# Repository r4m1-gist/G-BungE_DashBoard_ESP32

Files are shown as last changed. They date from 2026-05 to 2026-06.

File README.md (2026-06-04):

# G-BungE Dashboard ESP32

This project is an ESP32-based dashboard for the final Baja vehicle, Mk.5.
It aims to display vehicle status on 4-digit 7-segment modules using CAN data from the Sevcon Gen4 Size 6 controller.

Firmware and hardware resources for the G-BungE Mk.5 Baja EV dashboard.

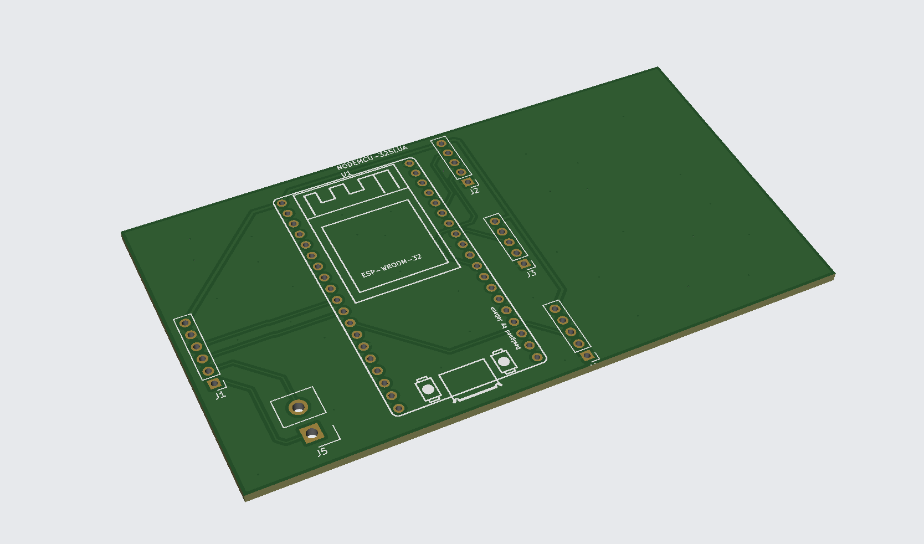
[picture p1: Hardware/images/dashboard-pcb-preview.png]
G-BungE Dashboard PCB preview


## Project Layout

```text
Firmware/
  main/
    main.ino

  test/
    ledsegmentcheck/
      ledsegmentcheck.ino

    soc_can_display/
      soc_can_display.ino

Hardware/
  README.md

  PCB KiCAD files/
    009_GBdashboard.kicad_pcb
    009_GBdashboard.kicad_pro
    009_GBdashboard.kicad_sch

    gerber/
      009_GBdashboard.zip
      info.md

  STEP files/
    DashBoard PLA Housing.step

  images/
    dashboard-pcb-preview.png
```

## Firmware

- `Firmware/main/main.ino`: main dashboard sketch for the Mk.5 vehicle
- `Firmware/test/ledsegmentcheck/ledsegmentcheck.ino`: basic check sketch for three 7-segment modules and CAN communication
- `Firmware/test/soc_can_display/soc_can_display.ino`: test sketch for displaying SoC, temperature, and voltage values received over CAN

## Hardware

- Controller: NodeMCU ESP32-S
- CAN transceiver: SN65HVD230
- Display: 4-digit 7-segment module x3
- PCB source: `Hardware/PCB KiCAD files/009_GBdashboard.kicad_pcb`, `Hardware/PCB KiCAD files/009_GBdashboard.kicad_sch`, `Hardware/PCB KiCAD files/009_GBdashboard.kicad_pro`
- Manufacturing export: `Hardware/PCB KiCAD files/gerber/009_GBdashboard.zip`
- 3D PLA housing: `Hardware/STEP files/DashBoard PLA Housing.step`

## Pin Map

### 7-Segment Display

| Part | SCLK | RCLK | DIO |
| --- | --- | --- | --- |
| SEG1 | GPIO21 | GPIO22 | GPIO17 |
| SEG2 | GPIO18 | GPIO19 | GPIO23 |
| SEG3 | GPIO13 | GPIO14 | GPIO25 |

### CAN

| Part | ESP32 Pin |
| --- | --- |
| CAN TXD / CTX | GPIO26 |
| CAN RXD / CRX | GPIO27 |

## CAN / Display Behavior

- CAN bus speed: 500 kbps
- Main sketch polls the Sevcon controller over CANopen SDO.
- Display 1 shows motor speed in rpm.
- Display 2 shows motor temperature in degrees Celsius.
- Test sketches are kept for segment wiring checks and CAN receive/display checks before vehicle installation.

## Notes

- Main firmware is built around the Sevcon Gen4 Size 6 controller used in the Mk.5 Baja EV.
- CAN bus termination should be 120 ohm only at each end of the bus.
- Segment display polarity can be adjusted in each sketch with `SEGMENT_ACTIVE_LOW`, `DIGIT_ACTIVE_HIGH`, and `SEND_SEGMENTS_FIRST`.
- Hardware PCB files were added under `Hardware/` for Mk.5 dashboard fabrication and reference.

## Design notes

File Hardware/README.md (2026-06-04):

# Hardware

Hardware resources for the G-BungE Mk.5 ESP32 dashboard.

G-BungE Dashboard PCB preview

## PCB KiCad Files

- Source files: `PCB KiCAD files/009_GBdashboard.kicad_pcb`, `PCB KiCAD files/009_GBdashboard.kicad_sch`, `PCB KiCAD files/009_GBdashboard.kicad_pro`
- Gerber export: `PCB KiCAD files/gerber/009_GBdashboard.zip`
- Made by quserunknownp.

## STEP Files

- Dashboard PLA housing: `STEP files/DashBoard PLA Housing.step`
- Made by r4m1.

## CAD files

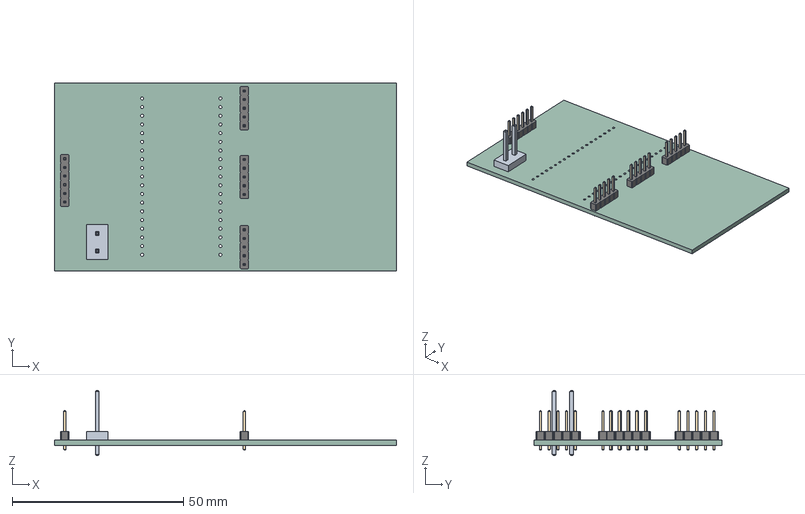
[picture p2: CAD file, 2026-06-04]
Hardware/STEP files/009_GBdashboard.step
100.0 x 55.0 x 19.1 mm
009_GBdashboard 1.1.1
PinHeader_1x05_P2.54mm_Vertical x 3
PinHeader_1x06_P2.54mm_Vertical
009_GBdashboard_PCB

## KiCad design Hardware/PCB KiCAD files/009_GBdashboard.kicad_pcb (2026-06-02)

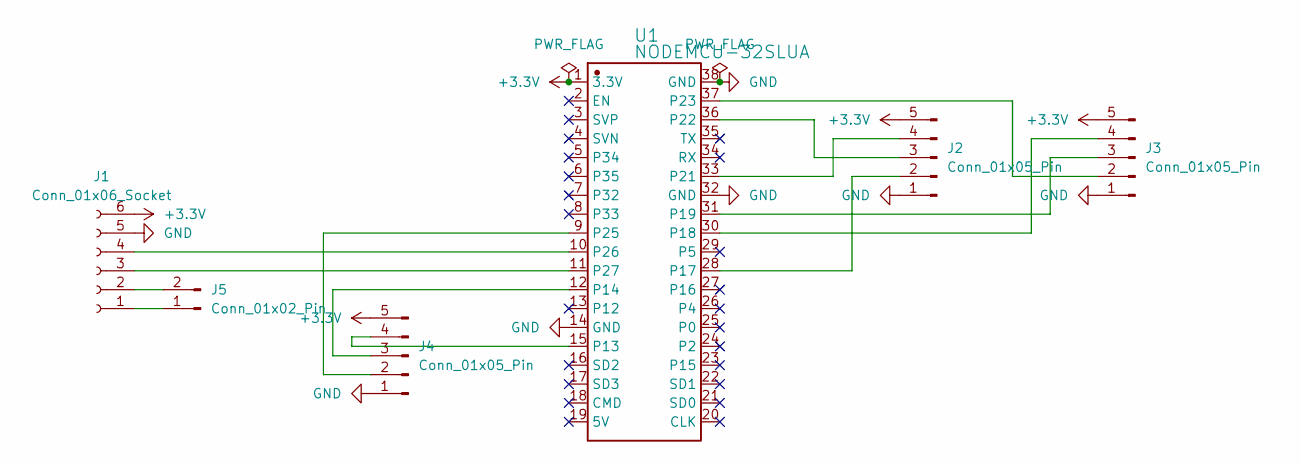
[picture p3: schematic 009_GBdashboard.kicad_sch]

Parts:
J1: Conn_01x06_Socket; PinHeader_1x06_P2.54mm_Vertical
J2, J3, J4: Conn_01x05_Pin; PinHeader_1x05_P2.54mm_Vertical
J5: Conn_01x02_Pin; Samtec_HPM-02-01-x-S_Straight_1x02_Pitch5.08mm
U1: NODEMCU-32SLUA; COMM-TH_NODEMCU-32SLUA; Manufacturer Part NodeMCU-32SLua

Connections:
+3.3V: J1.6, J2.5, J3.5, J4.5, U1.1 (3.3V)
GND: J1.5, J2.1, J3.1, J4.1, U1.14 (GND), U1.32 (GND), U1.38 (GND)
unnamed: J1.1, J5.1
unnamed: J1.2, J5.2
unnamed: J1.3, U1.11 (P27)
unnamed: J1.4, U1.10 (P26)
unnamed: J2.2, U1.28 (P17)
unnamed: J2.3, U1.36 (P22)
unnamed: J2.4, U1.33 (P21)
unnamed: J3.2, U1.37 (P23)
unnamed: J3.3, U1.31 (P19)
unnamed: J3.4, U1.30 (P18)
unnamed: J4.2, U1.9 (P25)
unnamed: J4.3, U1.12 (P14)
unnamed: J4.4, U1.15 (P13)

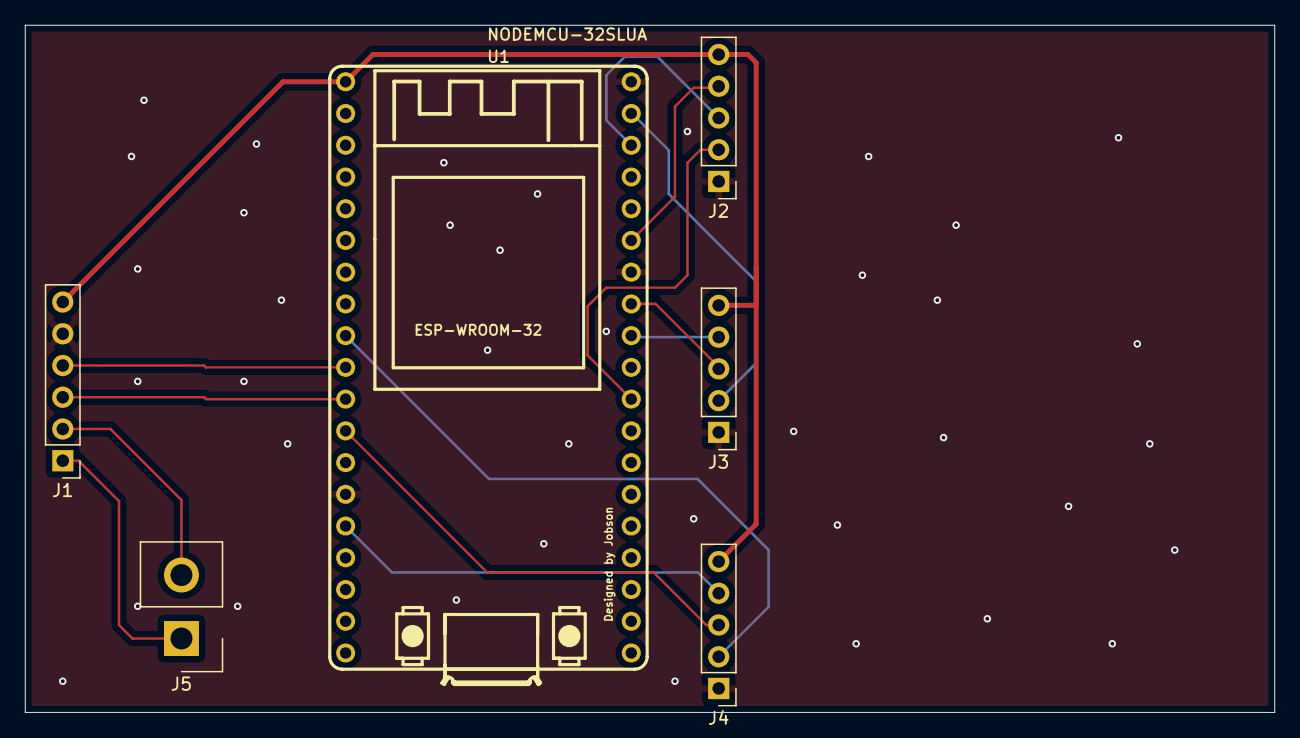
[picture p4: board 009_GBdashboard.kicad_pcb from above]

Board: 2 copper layers, 100.0 x 55.0 mm, 6 parts (0 on the bottom side), 15 nets.

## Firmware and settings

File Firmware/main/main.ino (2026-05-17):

/*
  G-BungE dashboard main sketch for Sevcon Gen4 Size 6

  Reads motor speed and motor temperature from the Sevcon over CANopen SDO.

  Display mapping:
    DISP1: motor speed, rpm, absolute value, 0..9999
    DISP2: motor temperature, degC, 0..9999

  Sevcon Gen4 manual notes:
    - Motor torque/speed are available in the 0x6000..0x67FF object range.
    - CiA 402 velocity actual value is commonly 0x606C:00.
    - Motor measurements including temperature are at object 0x4600.
    - The manual mentions motor temperature via 0x4600 sub 16 for CAN based thermistor use.

  If DVT maps these values to a TPDO later, this sketch can be changed to parse that
  PDO directly. SDO polling is intentionally used here so the dashboard can pull the
  values without depending on a preconfigured TPDO.
*/

#include <Arduino.h>
#include "freertos/FreeRTOS.h"
#include "driver/twai.h"

struct SegmentPins {
  uint8_t sclk;
  uint8_t rclk;
  uint8_t dio;
};

struct CanOpenObject {
  uint16_t index;
  uint8_t subIndex;
};

enum class PendingRequest : uint8_t {
  NONE,
  SPEED,
  MOTOR_TEMP
};

static const SegmentPins DISP1 = {21, 22, 17};
static const SegmentPins DISP2 = {18, 19, 23};

static const uint8_t CAN_TX_PIN = 26;
static const uint8_t CAN_RX_PIN = 27;

static const uint8_t SEVCON_NODE_ID = 1;
static const uint32_t SDO_REQUEST_ID = 0x600 + SEVCON_NODE_ID;
static const uint32_t SDO_RESPONSE_ID = 0x580 + SEVCON_NODE_ID;

static const CanOpenObject MOTOR_SPEED_OBJECT = {0x606C, 0x00};
static const CanOpenObject MOTOR_TEMP_OBJECT = {0x4600, 0x16};

static const uint32_t SDO_POLL_INTERVAL_MS = 100;
static const uint32_t SDO_RESPONSE_TIMEOUT_MS = 250;
static const uint32_t VALUE_TIMEOUT_MS = 2000;
static const uint32_t DISPLAY_REFRESH_INTERVAL_US = 1200;

static const bool SEGMENT_ACTIVE_LOW = true;
static const bool DIGIT_ACTIVE_HIGH = true;
static const bool SEND_SEGMENTS_FIRST = true;
static const uint16_t DIGIT_REFRESH_US = 250;

static uint16_t speedDisplayValue = 0;
static uint16_t tempDisplayValue = 0;
static uint8_t displayPosition = 0;
static uint32_t lastDisplayRefreshUs = 0;
static uint32_t lastPollMs = 0;
static uint32_t requestSentAtMs = 0;
static uint32_t lastValueRxMs = 0;
static uint32_t lastHeartbeatMs = 0;
static uint32_t canFrameCount = 0;
static uint32_t sdoAbortCount = 0;
static int32_t motorSpeedRpm = 0;
static int32_t motorTempC = 0;
static bool canReady = false;
static bool valuesReceived = false;
static PendingRequest pendingRequest = PendingRequest::NONE;
static PendingRequest nextRequest = PendingRequest::SPEED;

static const uint8_t SEG_A = 0b00000001;
static const uint8_t SEG_B = 0b00000010;
static const uint8_t SEG_C = 0b00000100;
static const uint8_t SEG_D = 0b00001000;
static const uint8_t SEG_E = 0b00010000;
static const uint8_t SEG_F = 0b00100000;
static const uint8_t SEG_G = 0b01000000;

static const uint8_t DIGITS[10] = {
  SEG_A | SEG_B | SEG_C | SEG_D | SEG_E | SEG_F,
  SEG_B | SEG_C,
  SEG_A | SEG_B | SEG_D | SEG_E | SEG_G,
  SEG_A | SEG_B | SEG_C | SEG_D | SEG_G,
  SEG_B | SEG_C | SEG_F | SEG_G,
  SEG_A | SEG_C | SEG_D | SEG_F | SEG_G,
  SEG_A | SEG_C | SEG_D | SEG_E | SEG_F | SEG_G,
  SEG_A | SEG_B | SEG_C,
  SEG_A | SEG_B | SEG_C | SEG_D | SEG_E | SEG_F | SEG_G,
  SEG_A | SEG_B | SEG_C | SEG_D | SEG_F | SEG_G
};

static const uint8_t DIGIT_SELECT[4] = {
  0b00001000,
  0b00000100,
  0b00000010,
  0b00000001
};

uint8_t normalizeSegments(uint8_t pattern) {
  return SEGMENT_ACTIVE_LOW ? ~pattern : pattern;
}

uint8_t normalizeDigitSelect(uint8_t digitMask) {
  return DIGIT_ACTIVE_HIGH ? digitMask : ~digitMask;
}

void writeTwoBytes(const SegmentPins &pins, uint8_t segments, uint8_t digitSelect) {
  digitalWrite(pins.rclk, LOW);

  if (SEND_SEGMENTS_FIRST) {
    shiftOut(pins.dio, pins.sclk, MSBFIRST, normalizeSegments(segments));
    shiftOut(pins.dio, pins.sclk, MSBFIRST, normalizeDigitSelect(digitSelect));
  } else {
    shiftOut(pins.dio, pins.sclk, MSBFIRST, normalizeDigitSelect(digitSelect));
    shiftOut(pins.dio, pins.sclk, MSBFIRST, normalizeSegments(segments));
  }

  digitalWrite(pins.rclk, HIGH);
}

void clearDisplay(const SegmentPins &pins) {
  writeTwoBytes(pins, 0x00, 0x00);
}

void refreshDigit(const SegmentPins &pins, uint8_t position, uint8_t number) {
  writeTwoBytes(pins, DIGITS[number], DIGIT_SELECT[position]);
  delayMicroseconds(DIGIT_REFRESH_US);
  clearDisplay(pins);
}

uint16_t clampDisplayValue(int32_t value) {
  if (value < 0) {
    value = -value;
  }
  if (value > 9999) {
    return 9999;
  }
  return (uint16_t)value;
}

void refreshDisplays() {
  uint32_t nowUs = micros();
  if (nowUs - lastDisplayRefreshUs < DISPLAY_REFRESH_INTERVAL_US) {
    return;
  }

  lastDisplayRefreshUs = nowUs;

  uint8_t speedDigits[4] = {
    (uint8_t)((speedDisplayValue / 1000) % 10),
    (uint8_t)((speedDisplayValue / 100) % 10),
    (uint8_t)((speedDisplayValue / 10) % 10),
    (uint8_t)(speedDisplayValue % 10)
  };
  uint8_t tempDigits[4] = {
    (uint8_t)((tempDisplayValue / 1000) % 10),
    (uint8_t)((tempDisplayValue / 100) % 10),
    (uint8_t)((tempDisplayValue / 10) % 10),
    (uint8_t)(tempDisplayValue % 10)
  };

  refreshDigit(DISP1, displayPosition, speedDigits[displayPosition]);
  refreshDigit(DISP2, displayPosition, tempDigits[displayPosition]);
  displayPosition = (displayPosition + 1) % 4;
}

bool startCan() {
  twai_general_config_t generalConfig = TWAI_GENERAL_CONFIG_DEFAULT(
    (gpio_num_t)CAN_TX_PIN,
    (gpio_num_t)CAN_RX_PIN,
    TWAI_MODE_NORMAL
  );
  generalConfig.alerts_enabled = TWAI_ALERT_ERR_PASS | TWAI_ALERT_BUS_ERROR | TWAI_ALERT_BUS_OFF | TWAI_ALERT_RX_DATA;

  twai_timing_config_t timingConfig = TWAI_TIMING_CONFIG_500KBITS();
  twai_filter_config_t filterConfig = TWAI_FILTER_CONFIG_ACCEPT_ALL();

  esp_err_t installResult = twai_driver_install(&generalConfig, &timingConfig, &filterConfig);
  if (installResult != ESP_OK) {
    Serial.print("[CAN] driver install failed: ");
    Serial.println(installResult);
    return false;
  }

  esp_err_t startResult = twai_start();
  if (startResult != ESP_OK) {
    Serial.print("[CAN] start failed: ");
    Serial.println(startResult);
    twai_driver_uninstall();
    return false;
  }

  Serial.println("[CAN] started at 500 kbps");
  return true;
}

void sendNmtOperational() {
  twai_message_t message = {};
  message.identifier = 0x000;
  message.data_length_code = 2;
  message.data[0] = 0x01;
  message.data[1] = SEVCON_NODE_ID;

  esp_err_t result = twai_transmit(&message, pdMS_TO_TICKS(20));
  Serial.print("[CANopen] NMT operational node=");
  Serial.print(SEVCON_NODE_ID);
  Serial.print(" result=");
  Serial.println(result);
}

CanOpenObject objectForRequest(PendingRequest request) {
  if (request == PendingRequest::MOTOR_TEMP) {
    return MOTOR_TEMP_OBJECT;
  }
  return MOTOR_SPEED_OBJECT;
}

const char *labelForRequest(PendingRequest request) {
  if (request == PendingRequest::MOTOR_TEMP) {
    return "motorTemp";
  }
  if (request == PendingRequest::SPEED) {
    return "speed";
  }
  return "none";
}

void advanceNextRequest(PendingRequest completedRequest) {
  nextRequest = (completedRequest == PendingRequest::SPEED) ? PendingRequest::MOTOR_TEMP : PendingRequest::SPEED;
}

bool sendSdoRead(PendingRequest request) {
  CanOpenObject object = objectForRequest(request);

  twai_message_t message = {};
  message.identifier = SDO_REQUEST_ID;
  message.data_length_code = 8;
  message.data[0] = 0x40;
  message.data[1] = object.index & 0xFF;
  message.data[2] = object.index >> 8;
  message.data[3] = object.subIndex;
  message.data[4] = 0x00;
  message.data[5] = 0x00;
  message.data[6] = 0x00;
  message.data[7] = 0x00;

  esp_err_t result = twai_transmit(&message, pdMS_TO_TICKS(20));
  if (result != ESP_OK) {
    Serial.print("[SDO] request failed ");
    Serial.print(labelForRequest(request));
    Serial.print(" result=");
    Serial.println(result);
    return false;
  }

  pendingRequest = request;
  requestSentAtMs = millis();
  return true;
}

int32_t readSdoSignedValue(const twai_message_t &message) {
  switch (message.data[0]) {
    case 0x4F:
      return (int8_t)message.data[4];
    case 0x4B:
      return (int16_t)((uint16_t)message.data[4] | ((uint16_t)message.data[5] << 8));
    case 0x43:
      return (int32_t)((uint32_t)message.data[4] |
                       ((uint32_t)message.data[5] << 8) |
                       ((uint32_t)message.data[6] << 16) |
                       ((uint32_t)message.data[7] << 24));
    default:
      return 0;
  }
}

uint32_t readSdoAbortCode(const twai_message_t &message) {
  return (uint32_t)message.data[4] |
         ((uint32_t)message.data[5] << 8) |
         ((uint32_t)message.data[6] << 16) |
         ((uint32_t)message.data[7] << 24);
}

void handleSdoResponse(const twai_message_t &message) {
  if (message.data_length_code < 8) {
    return;
  }

  uint16_t index = (uint16_t)message.data[1] | ((uint16_t)message.data[2] << 8);
  uint8_t subIndex = message.data[3];
  CanOpenObject expected = objectForRequest(pendingRequest);

  if (pendingRequest == PendingRequest::NONE || index != expected.index || subIndex != expected.subIndex) {
    return;
  }

  if (message.data[0] == 0x80) {
    sdoAbortCount++;
    Serial.print("[SDO] abort ");
    Serial.print(labelForRequest(pendingRequest));
    Serial.print(" object=0x");
    Serial.print(index, HEX);
    Serial.print(":");
    Serial.print(subIndex, HEX);
    Serial.print(" code=0x");
    Serial.println(readSdoAbortCode(message), HEX);
    advanceNextRequest(pendingRequest);
    pendingRequest = PendingRequest::NONE;
    return;
  }

  if (message.data[0] != 0x4F && message.data[0] != 0x4B && message.data[0] != 0x43) {
    Serial.print("[SDO] unsupported response command=0x");
    Serial.println(message.data[0], HEX);
    pendingRequest = PendingRequest::NONE;
    return;
  }

  int32_t value = readSdoSignedValue(message);
  if (pendingRequest == PendingRequest::SPEED) {
    motorSpeedRpm = value;
    speedDisplayValue = clampDisplayValue(motorSpeedRpm);
    advanceNextRequest(pendingRequest);
  } else if (pendingRequest == PendingRequest::MOTOR_TEMP) {
    motorTempC = value;
    tempDisplayValue = clampDisplayValue(motorTempC);
    advanceNextRequest(pendingRequest);
  }

  valuesReceived = true;
  lastValueRxMs = millis();
  pendingRequest = PendingRequest::NONE;
}

void receiveCanFrames() {
  twai_message_t message = {};

  while (twai_receive(&message, 0) == ESP_OK) {
    canFrameCount++;

    if (!message.extd && message.identifier == SDO_RESPONSE_ID) {
      handleSdoResponse(message);
    }
  }
}

void pollSevconObjects() {
  uint32_t nowMs = millis();

  if (pendingRequest != PendingRequest::NONE) {
    if (nowMs - requestSentAtMs > SDO_RESPONSE_TIMEOUT_MS) {
      Serial.print("[SDO] timeout ");
      Serial.println(labelForRequest(pendingRequest));
      advanceNextRequest(pendingRequest);
      pendingRequest = PendingRequest::NONE;
    }
    return;
  }

  if (nowMs - lastPollMs < SDO_POLL_INTERVAL_MS) {
    return;
  }

  lastPollMs = nowMs;
  sendSdoRead(nextRequest);
}

void printCanStatus() {
  twai_status_info_t status = {};
  if (twai_get_status_info(&status) != ESP_OK) {
    return;
  }

  Serial.print(" state=");
  switch (status.state) {
    case TWAI_STATE_STOPPED:
      Serial.print("STOPPED");
      break;
    case TWAI_STATE_RUNNING:
      Serial.print("RUNNING");
      break;
    case TWAI_STATE_BUS_OFF:
      Serial.print("BUS_OFF");
      break;
    case TWAI_STATE_RECOVERING:
      Serial.print("RECOVERING");
      break;
    default:
      Serial.print("UNKNOWN");
      break;
  }

  Serial.print(" rxErr=");
  Serial.print(status.rx_error_counter);
  Serial.print(" txErr=");
  Serial.print(status.tx_error_counter);
  Serial.print(" rxQueue=");
  Serial.print(status.msgs_to_rx);
}

void setupDisplayPins() {
  pinMode(DISP1.sclk, OUTPUT);
  pinMode(DISP1.rclk, OUTPUT);
  pinMode(DISP1.dio, OUTPUT);
  pinMode(DISP2.sclk, OUTPUT);
  pinMode(DISP2.rclk, OUTPUT);
  pinMode(DISP2.dio, OUTPUT);

  digitalWrite(DISP1.sclk, LOW);
  digitalWrite(DISP1.rclk, LOW);
  digitalWrite(DISP1.dio, LOW);
  digitalWrite(DISP2.sclk, LOW);
  digitalWrite(DISP2.rclk, LOW);
  digitalWrite(DISP2.dio, LOW);

  clearDisplay(DISP1);
  clearDisplay(DISP2);
}

void setup() {
  Serial.begin(115200);
  delay(300);

  Serial.println();
  Serial.println("G-BungE dashboard Sevcon Gen4 main");
  Serial.print("Sevcon CANopen node ID: ");
  Serial.println(SEVCON_NODE_ID);
  Serial.print("CAN TX/RX: GPIO");
  Serial.print(CAN_TX_PIN);
  Serial.print(" / GPIO");
  Serial.println(CAN_RX_PIN);
  Serial.print("Speed object: 0x");
  Serial.print(MOTOR_SPEED_OBJECT.index, HEX);
  Serial.print(":");
  Serial.println(MOTOR_SPEED_OBJECT.subIndex, HEX);
  Serial.print("Motor temp object: 0x");
  Serial.print(MOTOR_TEMP_OBJECT.index, HEX);
  Serial.print(":");
  Serial.println(MOTOR_TEMP_OBJECT.subIndex, HEX);

  setupDisplayPins();
  canReady = startCan();

  if (canReady) {
    sendNmtOperational();
    Serial.println("[SDO] polling Sevcon speed and motor temperature");
  }
}

void loop() {
  refreshDisplays();

  if (!canReady) {
    speedDisplayValue = 0;
    tempDisplayValue = 0;
    return;
  }

  receiveCanFrames();
  pollSevconObjects();

  if (valuesReceived && millis() - lastValueRxMs > VALUE_TIMEOUT_MS) {
    Serial.println("[SDO] value timeout: no recent Sevcon object responses");
    valuesReceived = false;
  }

  if (millis() - lastHeartbeatMs >= 1000) {
    lastHeartbeatMs = millis();
    Serial.print("[CAN] frames=");
    Serial.print(canFrameCount);
    Serial.print(" aborts=");
    Serial.print(sdoAbortCount);
    Serial.print(" speed=");
    Serial.print(motorSpeedRpm);
    Serial.print("rpm temp=");
    Serial.print(motorTempC);
    Serial.print("C");
    printCanStatus();
    Serial.println();
  }
}

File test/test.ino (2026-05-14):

/*
  NodeMCU ESP32-S dual 4-digit 7-segment + LED smoke test

  7-segment module pins:
    VCC, SCLK, RCLK, DIO, GND

  Pin map:
    VCC  -> ESP32 3V3 first, or 5V only if the module requires it
    SEG1 SCLK -> ESP32 GPIO21
    SEG1 RCLK -> ESP32 GPIO22
    SEG1 DIO  -> ESP32 GPIO17
    SEG2 SCLK -> ESP32 GPIO18
    SEG2 RCLK -> ESP32 GPIO19
    SEG2 DIO  -> ESP32 GPIO23
    GND  -> ESP32 GND

  Simple LEDs:
    LED1 -> ESP32 GPIO13 -> resistor -> LED+ / LED- -> GND
    LED2 -> ESP32 GPIO14 -> resistor -> LED+ / LED- -> GND
    LED3 -> ESP32 GPIO25 -> resistor -> LED+ / LED- -> GND

  CAN transceiver, for later:
    SN65HVD230 TXD / CTX -> ESP32 GPIO26
    SN65HVD230 RXD / CRX -> ESP32 GPIO27
    SN65HVD230 VCC       -> ESP32 3V3
    SN65HVD230 GND       -> ESP32 GND
    CANH-CANL            -> 120 ohm only at each end of the CAN bus
*/

#include <Arduino.h>
#include "freertos/FreeRTOS.h"
#include "driver/twai.h"

struct SegmentPins {
  uint8_t sclk;
  uint8_t rclk;
  uint8_t dio;
};

static const SegmentPins SEG1 = {21, 22, 17};
static const SegmentPins SEG2 = {18, 19, 23};

static const uint8_t LED_PINS[3] = {13, 14, 25};

static const uint8_t CAN_TX_PIN = 26;
static const uint8_t CAN_RX_PIN = 27;
static const uint32_t CAN_SEND_INTERVAL_MS = 1000;
static const uint32_t DISPLAY_REFRESH_INTERVAL_US = 1200;

// Change these if your module displays inverted/garbled output.
static const bool SEGMENT_ACTIVE_LOW = true;
static const bool DIGIT_ACTIVE_HIGH = true;
static const bool SEND_SEGMENTS_FIRST = true;

static const uint16_t COUNT_HOLD_MS = 100;
static const uint16_t DIGIT_REFRESH_US = 250;
static uint16_t displayValue = 0;
static uint8_t displayPosition = 0;
static uint32_t lastDisplayRefreshUs = 0;
static uint32_t lastCountMs = 0;
static uint32_t lastCanSendMs = 0;
static uint32_t canTxCounter = 0;
static bool canReady = false;

// Common segment bit order: bit0=a, bit1=b, ... bit6=g, bit7=dp.
static const uint8_t SEG_A  = 0b00000001;
static const uint8_t SEG_B  = 0b00000010;
static const uint8_t SEG_C  = 0b00000100;
static const uint8_t SEG_D  = 0b00001000;
static const uint8_t SEG_E  = 0b00010000;
static const uint8_t SEG_F  = 0b00100000;
static const uint8_t SEG_G  = 0b01000000;
static const uint8_t SEG_DP = 0b10000000;

static const uint8_t DIGITS[10] = {
  SEG_A | SEG_B | SEG_C | SEG_D | SEG_E | SEG_F,          // 0
  SEG_B | SEG_C,                                          // 1
  SEG_A | SEG_B | SEG_D | SEG_E | SEG_G,                  // 2
  SEG_A | SEG_B | SEG_C | SEG_D | SEG_G,                  // 3
  SEG_B | SEG_C | SEG_F | SEG_G,                          // 4
  SEG_A | SEG_C | SEG_D | SEG_F | SEG_G,                  // 5
  SEG_A | SEG_C | SEG_D | SEG_E | SEG_F | SEG_G,          // 6
  SEG_A | SEG_B | SEG_C,                                  // 7
  SEG_A | SEG_B | SEG_C | SEG_D | SEG_E | SEG_F | SEG_G,  // 8
  SEG_A | SEG_B | SEG_C | SEG_D | SEG_F | SEG_G           // 9
};

// Left to right digit select bits.
static const uint8_t DIGIT_SELECT[4] = {
  0b00001000,
  0b00000100,
  0b00000010,
  0b00000001
};

uint8_t normalizeSegments(uint8_t pattern) {
  return SEGMENT_ACTIVE_LOW ? ~pattern : pattern;
}

uint8_t normalizeDigitSelect(uint8_t digitMask) {
  return DIGIT_ACTIVE_HIGH ? digitMask : ~digitMask;
}

void writeTwoBytes(const SegmentPins &pins, uint8_t segments, uint8_t digitSelect) {
  digitalWrite(pins.rclk, LOW);

  if (SEND_SEGMENTS_FIRST) {
    shiftOut(pins.dio, pins.sclk, MSBFIRST, normalizeSegments(segments));
    shiftOut(pins.dio, pins.sclk, MSBFIRST, normalizeDigitSelect(digitSelect));
  } else {
    shiftOut(pins.dio, pins.sclk, MSBFIRST, normalizeDigitSelect(digitSelect));
    shiftOut(pins.dio, pins.sclk, MSBFIRST, normalizeSegments(segments));
  }

  digitalWrite(pins.rclk, HIGH);
}

void clearDisplay(const SegmentPins &pins) {
  writeTwoBytes(pins, 0x00, 0x00);
}

void refreshDigit(const SegmentPins &pins, uint8_t position, uint8_t number) {
  writeTwoBytes(pins, DIGITS[number], DIGIT_SELECT[position]);
  delayMicroseconds(DIGIT_REFRESH_US);
  clearDisplay(pins);
}

void setSequentialLed(uint16_t value) {
  uint8_t activeLed = value % 3;

  for (uint8_t index = 0; index < 3; index++) {
    digitalWrite(LED_PINS[index], index == activeLed ? HIGH : LOW);
  }
}

void showNumberFor(uint16_t value, uint16_t holdMs) {
  uint8_t displayDigits[4] = {
    (uint8_t)((value / 1000) % 10),
    (uint8_t)((value / 100) % 10),
    (uint8_t)((value / 10) % 10),
    (uint8_t)(value % 10)
  };

  uint32_t startedAt = millis();

  while (millis() - startedAt < holdMs) {
    for (uint8_t pos = 0; pos < 4; pos++) {
      refreshDigit(SEG1, pos, displayDigits[pos]);
      refreshDigit(SEG2, pos, displayDigits[pos]);
    }
  }
}

void lampTestFor(uint16_t holdMs) {
  uint32_t startedAt = millis();

  while (millis() - startedAt < holdMs) {
    for (uint8_t pos = 0; pos < 4; pos++) {
      refreshDigit(SEG1, pos, 8);
      refreshDigit(SEG2, pos, 8);
    }
  }
}

void ledWalkTest() {
  for (uint8_t index = 0; index < 3; index++) {
    for (uint8_t clearIndex = 0; clearIndex < 3; clearIndex++) {
      digitalWrite(LED_PINS[clearIndex], LOW);
    }

    digitalWrite(LED_PINS[index], HIGH);
    Serial.print("[LED] testing LED");
    Serial.println(index + 1);
    delay(1000);
  }

  for (uint8_t index = 0; index < 3; index++) {
    digitalWrite(LED_PINS[index], LOW);
  }
}

void segmentPairTest() {
  Serial.println("[SEG1] lamp test only");
  uint32_t seg1StartedAt = millis();
  while (millis() - seg1StartedAt < 1500) {
    for (uint8_t pos = 0; pos < 4; pos++) {
      refreshDigit(SEG1, pos, 8);
    }
  }

  Serial.println("[SEG2] lamp test only");
  uint32_t seg2StartedAt = millis();
  while (millis() - seg2StartedAt < 1500) {
    for (uint8_t pos = 0; pos < 4; pos++) {
      refreshDigit(SEG2, pos, 8);
    }
  }
}

bool startCan() {
  twai_general_config_t generalConfig = TWAI_GENERAL_CONFIG_DEFAULT(
    (gpio_num_t)CAN_TX_PIN,
    (gpio_num_t)CAN_RX_PIN,
    TWAI_MODE_NORMAL
  );
  twai_timing_config_t timingConfig = TWAI_TIMING_CONFIG_500KBITS();
  twai_filter_config_t filterConfig = TWAI_FILTER_CONFIG_ACCEPT_ALL();

  esp_err_t installResult = twai_driver_install(&generalConfig, &timingConfig, &filterConfig);
  if (installResult != ESP_OK) {
    Serial.print("[CAN] driver install failed: ");
    Serial.println(installResult);
    return false;
  }

  esp_err_t startResult = twai_start();
  if (startResult != ESP_OK) {
    Serial.print("[CAN] start failed: ");
    Serial.println(startResult);
    twai_driver_uninstall();
    return false;
  }

  Serial.println("[CAN] started at 500 kbps");
  return true;
}
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

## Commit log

2026-05-09 Add ESP32 segment test sketch
2026-05-17 Organize Arduino dashboard sketches
2026-05-20 LED Segment Pin Change
2026-05-20 Document dashboard pin map
2026-06-04 Organize Fold
    [009_GBdashboard.kicad_pcb, 009_GBdashboard.kicad_sch, 009_GBdashboard.step]
